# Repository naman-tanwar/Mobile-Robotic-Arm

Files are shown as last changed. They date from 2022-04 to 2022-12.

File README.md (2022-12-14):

# Mobile Robotic Arm
A 3D-printed Robotic arm mounted on Aluminium 2020 chassis which can be controlled over the internet from anywhere in the world. Ideal for remote exploration.
## Abstract
Exploration of various unreachable/hazardous places is a key to scientifically enrich our understanding of this universe. And remotely performing operations on these locations opens more aspects of not even exploration but also providing medical aid where a real human intervention is not possible. This project aims to serve this goal of remote exploration and operation.

## Methodology
The working of the project can be defined as:
- 2 Ultrasonic sensors are used to measure the distance from any obstacle in any of the four directions.
- One of the Ultrasonic sensors is mounted on a servo motor which will help to measure the distance from a obstacle in 3 directions using only one sensor
- Wheels and the robot arms are controlled using ESP32 microcontroller
- A live camera is setup using Raspberry Pi which can be accessed remotely from any location. This makes the Robot perfect for operations in remote locations.
- The robot can be controlled remotely using blynk IoT Platform

## Mechanical Design and Implementaion
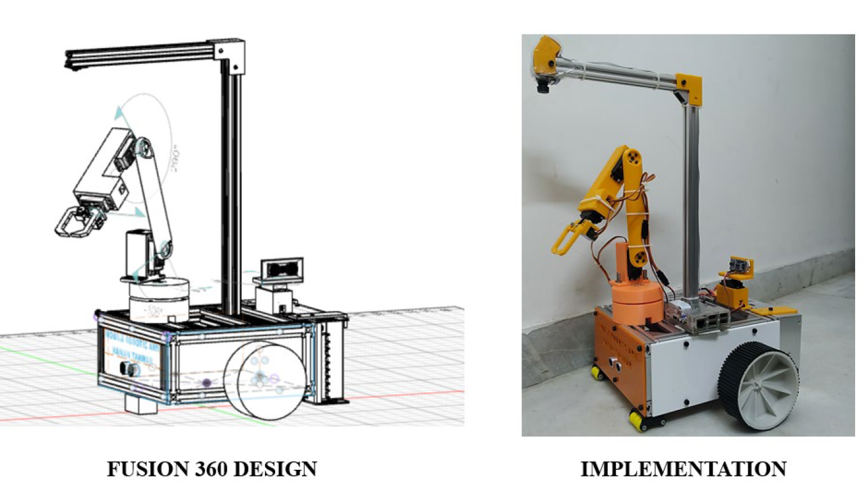
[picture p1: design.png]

## Circuit Diagram
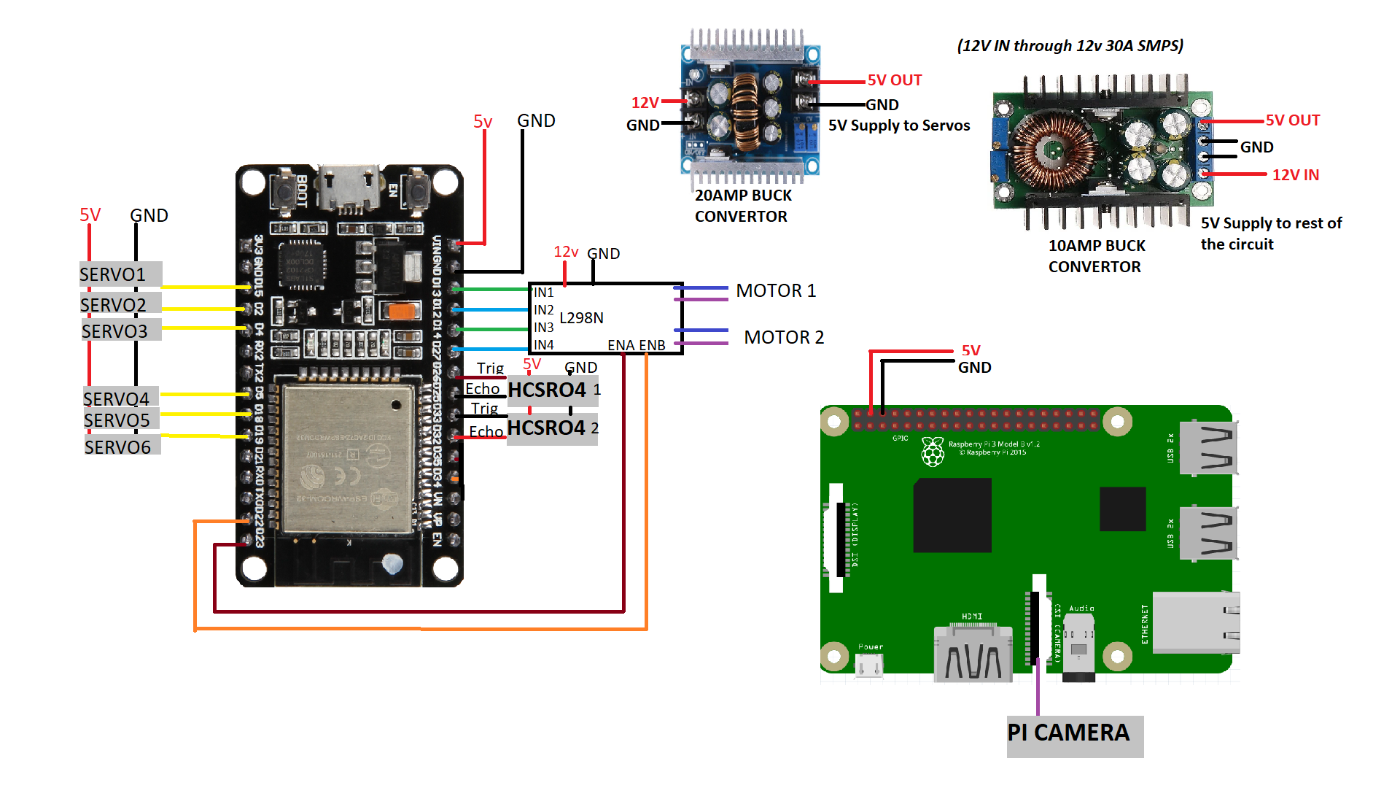
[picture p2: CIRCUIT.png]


### Power Supply
A 12V 30A rated SMPS is used to supply power to the entire system. Sisce this power supply is temporary, It can be replaced with a suitable LiPo battery (preferably, 3S 35C 3500MAh) for mobility.
The Volatage is then step down to 5v using Buck Covertors so that it can be used to power other components.
The servo (Tower Pro MG995) can pull upto 1.5A to 2A of current under stall condition. So all the 6 servers can pull upto 12A of current. Hence, a separate buck converter (rated 20A) is used to power servos alone. The remaining buck convertor (rated 10A) is used to power rest of the circuit.

### ESP32 and connected devices
ESP32 is used as a microcontroller as it has WiFi functionality which can be used to connect to the internet.
Six Tower Pro MG995 servos are connected to the digital pins of ESP32 Microcontroller (D2, D4, D5, D15, D18, D19). L298N Motor Driver is used to control two 200 RPM geared DC motor. The inputs are connected to D12, D13, D14, D27 while enable is connected to D23 and D22. Two HCSRO4 Ultrasonic senosrs are used to measure distance in all four direction. Digital Pins D25, D26, D32, D33 are used for connections of ultrasonic sensors.
### Raspberry Pi
A Raspberry Pi camera is connected to Raspberry Pi 3B+ which can be used to view camera preview remotely.
### Circuit Assembly
The circuit is made on a PCB board. Male header pins are used to connect the servo motors, Ultrasonic sensors, Motor Driver input and power input for Raspberry Pi. Femal headers are used to mount ESP 32 on the PCB.
In the top left, two Buck convertors can be seen mounted with some screws on the PCB.In the bottom, L298N motor driver is mounted with some screws.

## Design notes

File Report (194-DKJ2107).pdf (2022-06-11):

# A Custom-designed 3D Printed 4-DoF Mobile Robotic Arm for Remote Exploration

Naman Tanwar
School of Electronics Engineering Vellore Institute of Technology Vellore, Tamil Nadu, India naman.tanwar2020@vitstudent.ac.in

Sanjay Kumar Singh
School of Electronics Engineering Vellore Institute of Technology Vellore, Tamil Nadu, India sanjaykumar.singh@vit.ac.in

Abstract—Exploration of various unreachable/hazardous places is a key to scientifically enriching our understanding of this universe. And remotely performing operations on these locations opens more aspects of not even exploration but also providing medical aid where a real human intervention is not possible. This project aims to serve this goal of remote exploration and operation. A custom-designed 3D printed 4DoF Robotic arm is used for operations in the remote terrain with a movable rigid aluminum custom-designed chassis with multiple distance sensors and a camera for remote exploration and navigation.
Keywords—Robotic Arm, Mobile vehicle, Remotely Operated, ESP32, Raspberry Pi, Servo Motor, Blynk, Cloud service
I. INTRODUCTION
There are many places where human intervention is not possible simply because it might cost a human life. The requirement of intervening in those places might be to explore those parts of the world, to fix some critical faults at places where human intervention is very dangerous, to save another human life by providing medical aid, or for military reasons like spying on terrorist operations.
Hence to serve these purposes, this paper presents a project that aims to build a remotely controlled robot that can explore, navigate, operate, and can be manually controlled in such remote places.
This project is a 3D printed 4-DoF robotic arm mounted on a custom-designed Aluminium-based movable chassis with different sensors and a camera. Ultrasonic sensors are used to provide the available distance in all four directions and a camera is used to visually inspect the target on which the robot will operate. The whole construction can be controlled remotely via the internet. The only requirement is that that place should have mobile internet coverage. This can also affect the places it can operate but different modes of connectivity can be used according to the location where the robot will operate.

II. DESIGN AND IMPLEMENTAION
A. Methodology
The working of the project can be defined as:
- 2 Ultrasonic sensors are used to measure the distance from any obstacle in any of the four directions.
- The front Ultrasonic sensors will be used to measure the distance of the front obstacle. The distance can then be used by the robotic arm to operate on that obstacle
- The rear Ultrasonic sensors are mounted on a servo motor which will help to measure the distance from an obstacle in 3 directions using only one sensor
- Wheels and the robot arms are controlled using an ESP32 microcontroller
- A live camera is set up using Raspberry Pi which can be accessed remotely from any location. This makes the Robot perfect for operations in remote locations.
- The robot can be controlled remotely using the Blynk IoT Platform
Temporarily, a 12v SMPS is used instead of a LiPo battery to power the robot.
B. Mechanical Design and Implementation

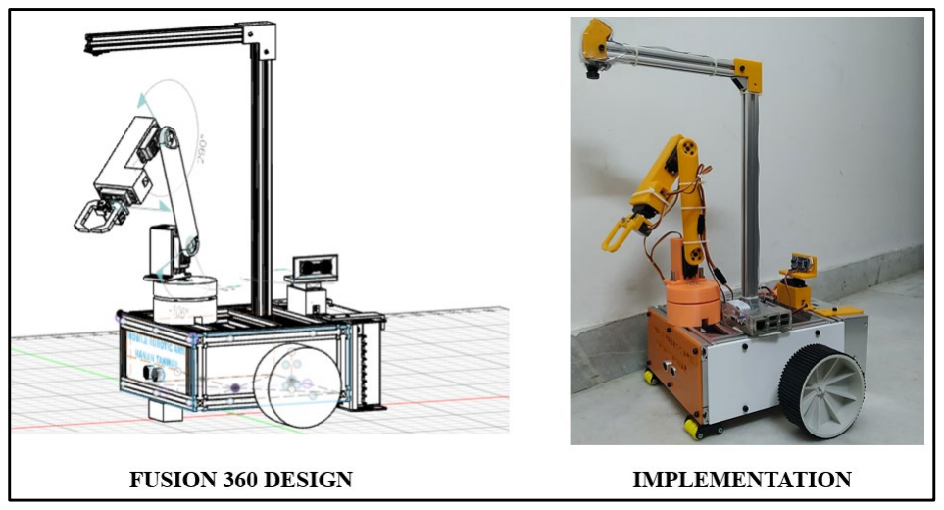
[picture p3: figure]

Fig. 1. Mechanical Design and Implementation
The complete mechanical structure is designed using Fusion 360 keeping in mind the real-world parameters such as servo motor size, motor diameter, wheel size, circuit board dimensions, power supply dimensions, the center of the movement, etc. About 14 individual parts were designed which then was 3d printed.
The robotic arm parts, sensor mount, and PCB mount were 3D printed with PLA filament.

DICKENSIAN JOURNAL

VOLUME 22, ISSUE 5, 2022

ISSN NO : 0012-2440

PAGE NO: 1764

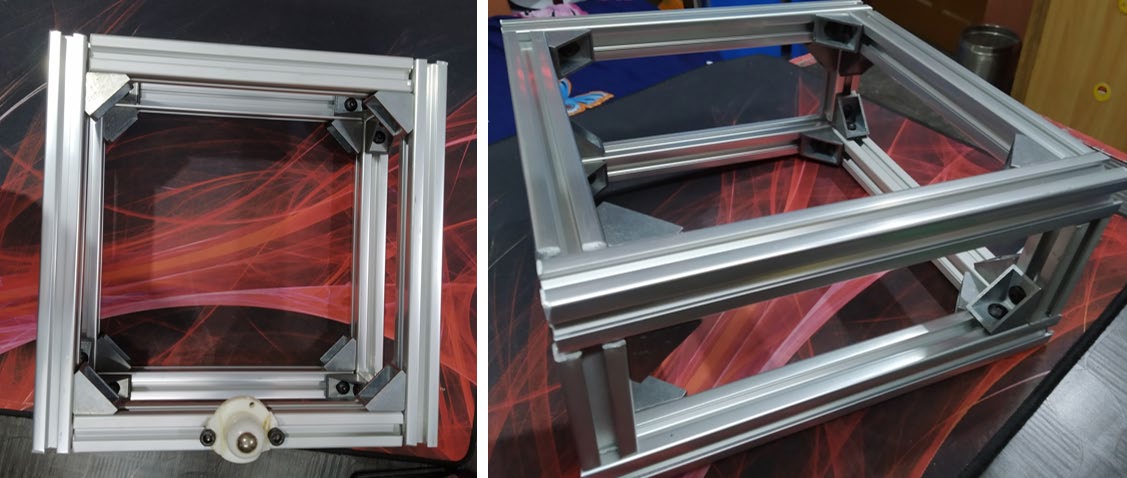
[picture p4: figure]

Fig. 2. Robot Chasis
The robot chassis was made using the 2020 Aluminium Extrusion profile. The profile was cut with an angle grinder according to the 3D design and then joined together with lead-based corner brackets. The mounts for the camera were also made using this aluminium profile.
The Camera is mounted horizontally to the ground to get a perfectly aligned 2D image of the ground which will be further useful for performing operations on the ground objects via the robotic arm.
The Orange and white colour acrylic sheet (as seen in Fig. 1) is also designed using Fusion 360 and then laser cut through an online service (www.Robu.in) to mount the front sensor and DC geared motors. [3]

Two 100rpm geared DC motors mounted on the orange acrylic sheets will be used as main motors to move the entire robot around.
Two wheels are attached to the geared motors to provide mobility. The motors with wheels are mounted horizontally centered concerning the complete chassis (this includes the width of the power supply).

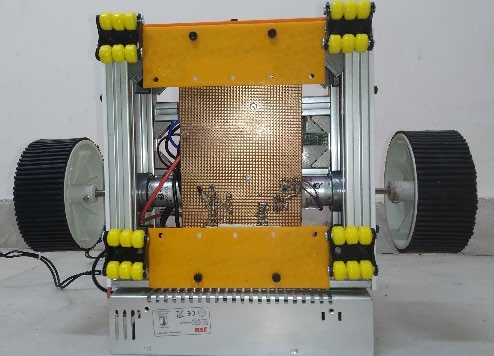
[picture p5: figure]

Fig. 3. Robot’s bottom view. 4 castor wheels, PCB board, 3D printed PCB holder plates, and 2 main 100mm wheels can be observed.
The wheel diameter is 100mm which lifted the whole chassis by 22mm and hence about 22mm castor wheels were used in front and back to provide stability to the robot
C. Circuit Diagram, Components used, and Circuit:

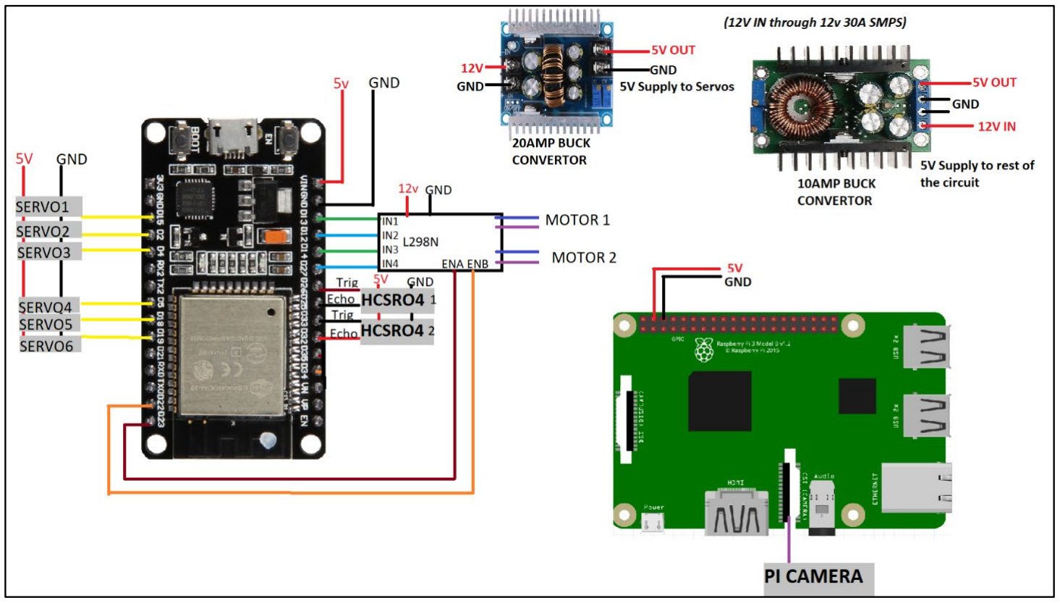
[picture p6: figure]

Fig. 4. Circuit Diagram

The Circuit has three parts:
- Power Supply
- ESP32 and connected devices
- Raspberry Pi and camera

1.Power Supply
A 12V 30A rated SMPS is used to supply power to the entire system. Since this power supply is temporary, It can be replaced with a suitable LiPo battery (preferably, 3S 35C 3500MAh) for mobility [7].
The voltage is then stepped down to 5v using Buck Converters so that it can be used to power other components.

The servo (Tower Pro MG995) can pull up to 1.5A to 2A of current under stall conditions. So all the 6 servers can pull up to 12A of current. Hence, a separate buck converter (rated 20A) is used to power servos alone. The remaining buck convertor (rated 10A) is used to power the rest of the circuit. ESP32 is used as a microcontroller as it has WiFi functionality which can be used to connect to the internet. A JioFi hotspot is used to connect to the internet. Since the JioFi hotspot is based on the mobile internet, the hotspot itself is mounted on the robot and hence there is no effect on the mobility of the robot
2.ESP32 and connected devices
Six Tower Pro MG995 servos are connected to the digital pins of the ESP32 Microcontroller (D2, D4, D5, D15, D18, D19). L298N Motor Driver is used to control two 200 RPM geared DC motors. The inputs are connected to D12, D13, D14, and D27 while enable is connected to D23 and D22. Two HCSRO4 Ultrasonic sensors are used to measure distance in all four directions. Digital Pins D25, D26, D32, and D33 are used for connections of ultrasonic sensor

3.Raspberry Pi and Camera
A Raspberry Pi camera is connected to Raspberry Pi 3B+ which can be used to view camera preview remotely.
The previously used 5v 10Amp buck convertor is used to directly power the raspberry pi through its GPIO pins.

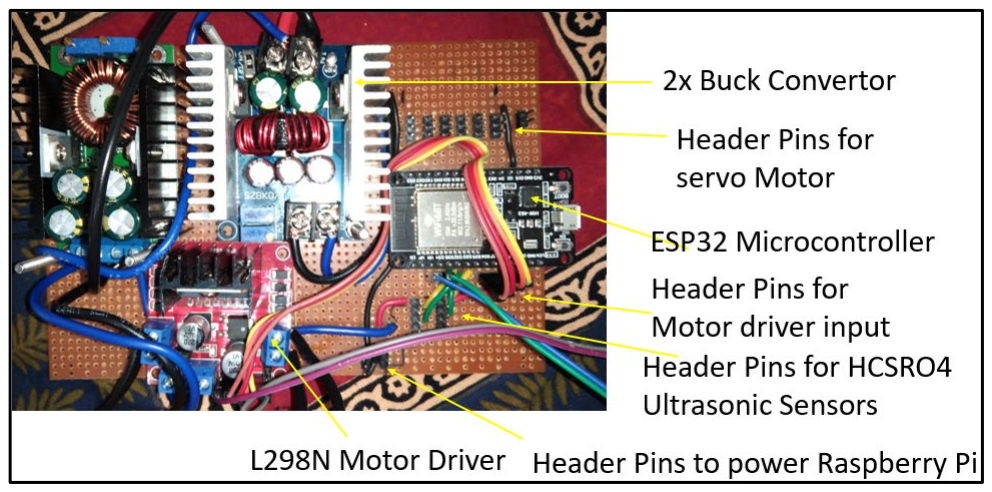
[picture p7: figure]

Fig. 5. Circuit
The circuit is made on a PCB board. Male header pins are used to connect the servo motors, Ultrasonic sensors, Motor Driver input, and power input for Raspberry Pi. Female headers are used to mount ESP 32 on the PCB.
Two Buck converters can be seen mounted with some screws on the PCB in the top left. At the bottom, the L298N motor driver is mounted with some screws.
D. Raspberry Pi Camera setup:
- A web interface is set up for the Raspberry Pi camera through an Open Source GitHub Project. But this can only be viewed locally. [2]
- Then, using the remote.it platform, the local webpage is streamed to the internet which can be accessed through a specific URL. [4]
- This URL is then used in the Blynk IoT platform to watch the video stream through the mobile app. [5]
E. Servo Calibration
- The MG995 servos used for the arm were not calibrated to move to a correct angle.
- For an input of 0 to 147 degrees (using Arduino IDE) the servo moved from 0 to 180 degrees. So, the servos were calibrated accordingly.
- The fully open and fully closed point for the servo used in the claw was found to be 180 and 140 respectively
F. Movement Equations

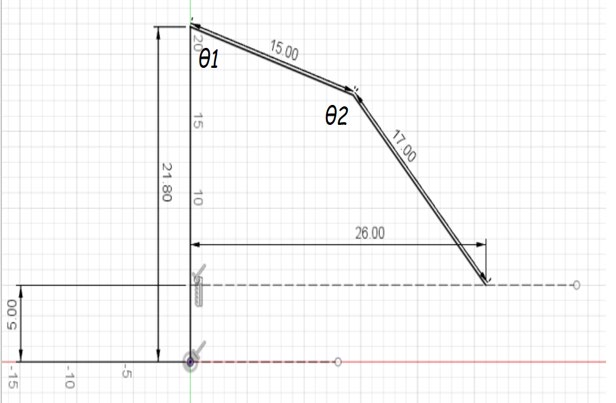
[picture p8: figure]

Fig. 6. 2D constrained sketch in Fusion 360
A 2D constrained line schematic was set up in Fusion 360. For different values of the horizontal distance, angle values were found which then was inserted into Microsoft Excel to find polynomial equations between the distance and the angle

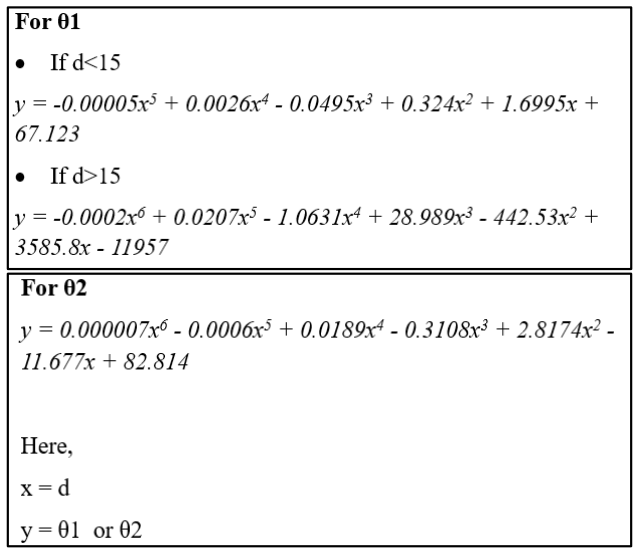
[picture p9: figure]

Fig. 7. Movement Equations

G. Mobile App using blynk

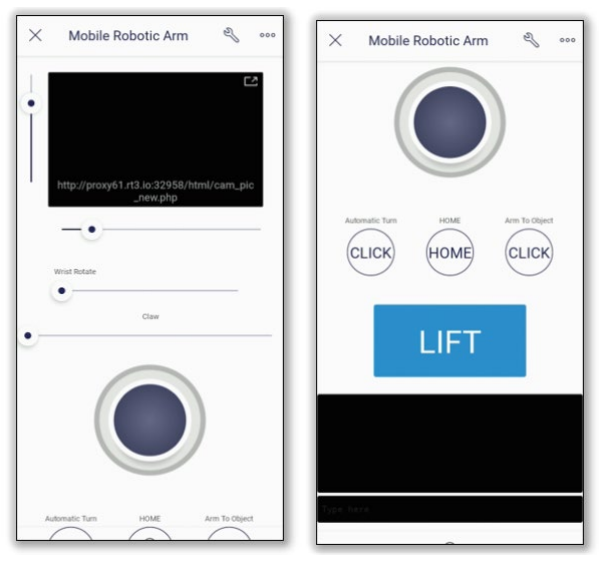
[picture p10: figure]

Fig. 8. Mobile App using Blynk IoT platform
The Blynk IoT provides IoT functionality to the robot. This platform also provides an app builder with which we can build our app using its provided widgets.
Features of our Mobile Application:
- Display for camera output
- Horizontal and Vertical Sliders to control Arm position
- Sliders to control Wrist Angle and Claw
- Joystick to move the Robot
- Buttons to perform some programmed operations such as Automatic Turn, Moving Arm to Object Location, and Home button to place arm to home location
- LIFT button to lift the arm up
- Terminal window to perform debugging.
H. ESP32 Code Flow chart and Explanation
The code for the ESP32 microcontroller is written in C++ inside Arduino IDE. Different extra libraries for the Blynk platform and servo control were also installed in the Arduino IDE. Since the code has more than 500 lines so only an explanation and flowchart are mentioned in this paper. The actual code can be viewed using the GitHub link provided in the references [1].

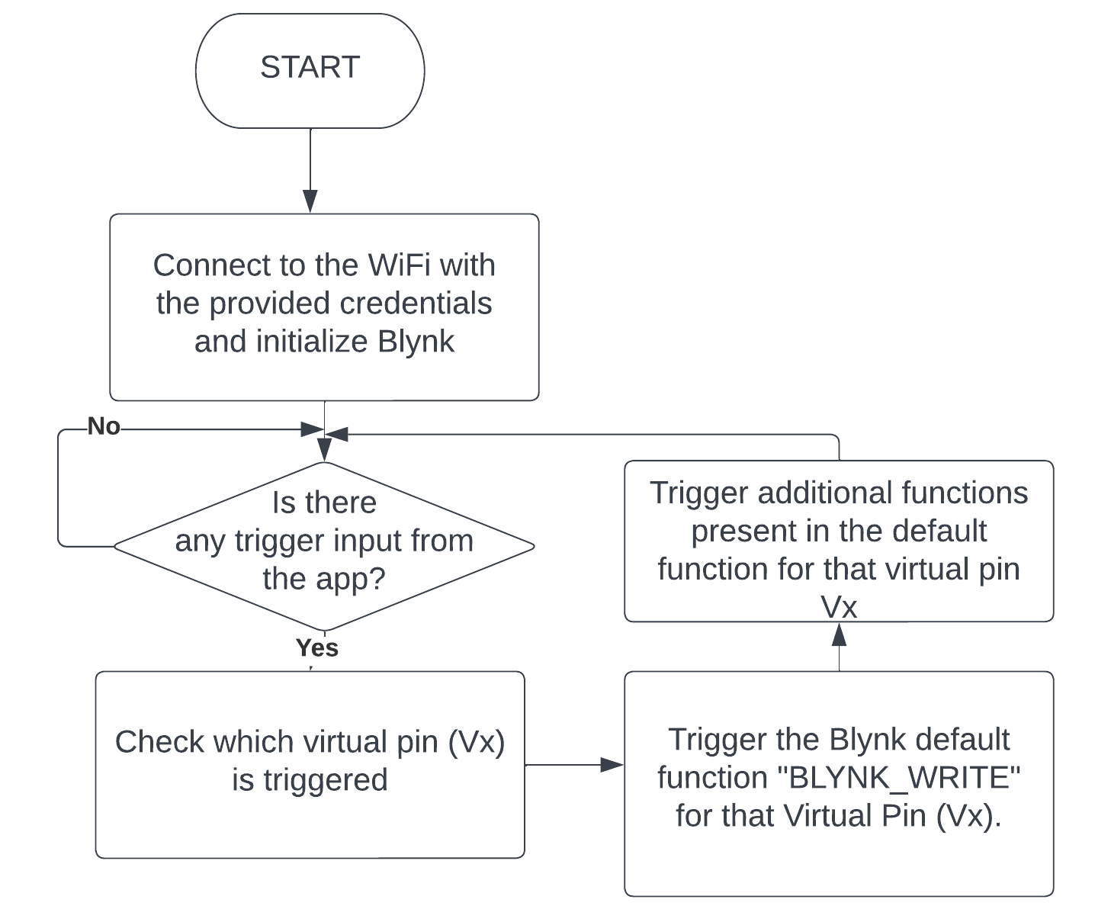
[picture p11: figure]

Fig. 9. Basic Flow Chart of the Operation
Initially, the ESP32 gets connected to the WiFi hotspot with the credentials provided in the code itself. Then the device looks for the trigger of any virtual pin through the application created using the Blynk platform.
Vx represents the Virtual Pin where ‘x’ stands for the pin-number. The various functions involved in the operation are listed in TABLE I.
TABLE I. Various Functions Triggered by the Virtual Pins and their Description
Virtual Pin/ Data Stream | Functional Description of BLYNK_WRITE (Vx) | Additional Functions Called during operation
V0 | Slider control for Base i.e., Horizontal Slider | BaseServoOperate() – Custom function to rotate base servo
V2 | Terminal Window | GetSensorData() – To get the data from both ultrasonic sensors
V3 | Joystick Control | FrontDist() – To get front sensor destance data forward(), backward(), right(), left(), Brake() – These functions control the 6 pins of the motor driver which then controls the 2 motors.
V4 | Vertical Slider | calcTheta(vertValue) – This will calculate theta based on the value of the vertical slider according to the formulae derived earlier.

V5 | Slider to Rotate Wrist | WristServoOperate() – To operate the wrist servo based on the slider value
V6 | Slider to operateClaw | ClawServoOperate() - To operate claw servo based on the slider value
V7 | Home Button | Home() – To make the servo go home positions as defined in the code.
V8 | AutoTurn Button | autoTurn() – This will initially calculate the distance in all 4 directions and then decide to rotate in the preferred direction.
V9 | ArmToObject Button | FrontDist() – To obtain a front distance value from the sensor calcTheta()- To calculate theta values based on the front sensor and then operate the servos BaseServoOperate() – To operate base servo
V10 | Lift Button | ArmServoOperate() – To rotate the servo based on the two angle values

III. WORKING DEMONSTRATION
A. Automatic Arm Movement Towards object

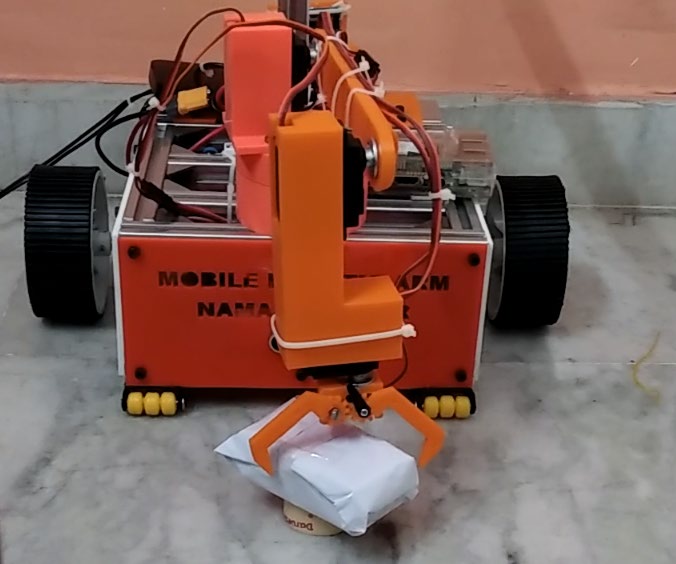
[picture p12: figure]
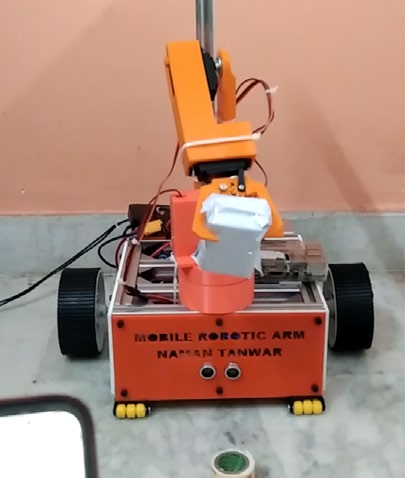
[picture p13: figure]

Fig. 10. Automatic Arm Movement and Object Lifting
When the ArmToObject button is pressed, the front Sensor finds the distance of the object from the robot which then is used to move the robotic arm. Then the object can be lifted just by clicking on the LIFT button on the mobile application.
B. Sensor readings through debug window

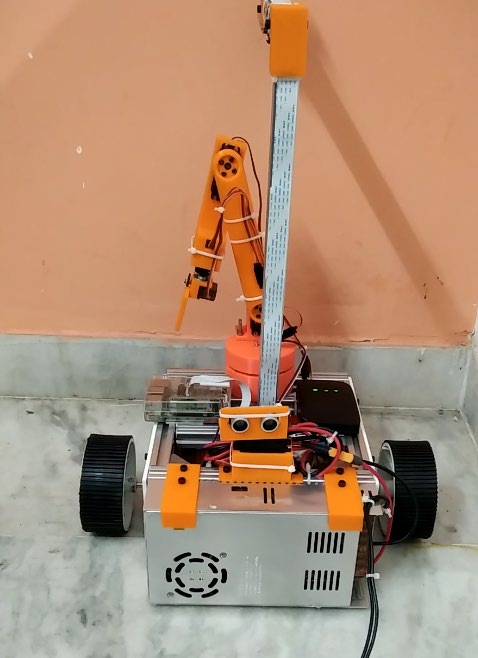
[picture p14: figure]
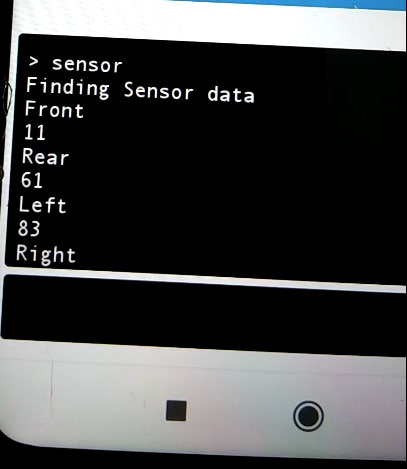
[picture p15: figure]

Fig. 11. Robot State and Sensor Readings
The robot is programmed as such if you enter “sensor” in the debug window then the robot will find the distance in all 4 directions and then displays it on the debug window itself.
C. Automatic Turn

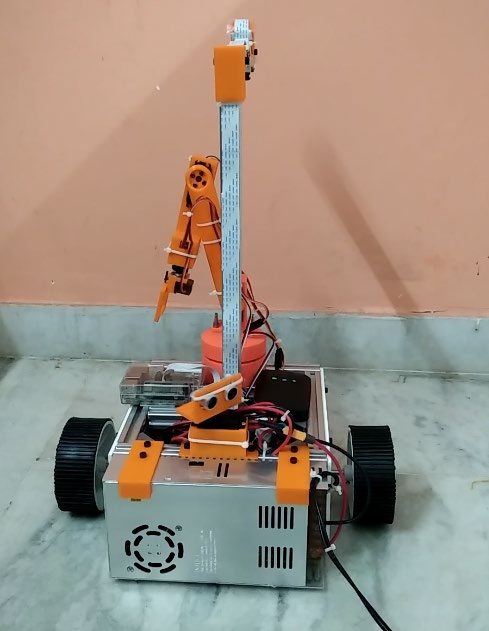
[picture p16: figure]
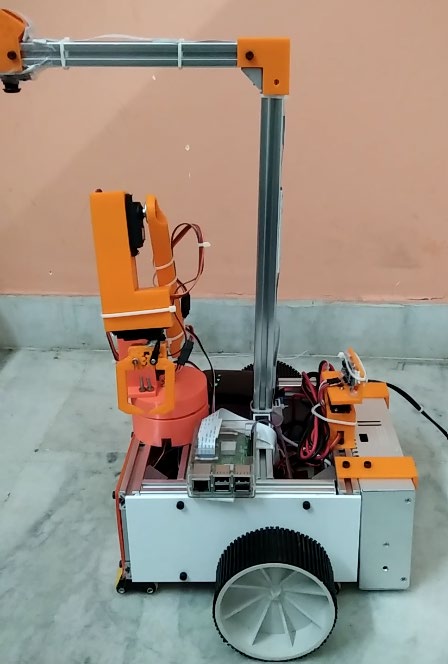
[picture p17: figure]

Fig. 12. Robot initial State and State after Turn Operation
When the Automatic Turn button is pressed, the robot will first find the distances in all 4 directions and then turn Right or Left based on the amount of distance available.
It was found out that when both the motors are spinning in the same rotational direction (clockwise/anticlockwise) with the same base speed (ie ~100rpm at ~12v), then it takes exactly 600ms to make a perpendicular rotation. Hence to turn left or right the motors were programmed to spin in clockwise or anticlockwise respectively for exactly 600ms. The entire robot’s operation can be viewed through the demonstration videos which can be viewed through the Google Drive link shared. [6]

IV. SUMMARY
In this paper, a practical model of the Mobile Robotic Arm was discussed. Initially, the complete robot was designed using Fusion 360 from which some parts were 3D printed including the parts for the Arm of the robot and structural support parts like PCB holder and power supply holder. The design gave an idea of how the real-world robot will look like and it also helped in constructing the Aluminum 2020 profile-based chassis and gave a layout for laser cutting the 3 acrylic sheets which were then used to mount the ultrasonic sensor and the motors
Then circuit was designed and built on a PCB board (Veroboard) keeping in mind the power requirements of every component. Temporarily a 12v SMPS was used which can easily be replaced with a suitable LiPo battery in the future.
Then the movement equations were practically derived, different moving parts were calibrated and finally, a suitable code for the ESP32 was written in C++ with different functions like Setting arm location using Sliders, Auto Arm to Object, Arm to Home, Lift Operation, Automatic Robot Turn operation, Joystick Movement and Getting data using terminal, using Arduino IDE.
Finally, the working of the complete project was demonstrated.
V. FUTURE IMPROVEMENTS
- Using LIPO battery instead of SMPS Supply
- Using better servos (rather than stepper motors) which are more precise, have zero gear dead-zone, and can handle more weight (This may require a major design change and implementation of gear system)
- Coding an automatic area map algorithm to perform a certain task in a remote area without human intervention
- Using LIDAR instead of Ultrasonic sensors to map the area
- Using image processing to identify the object with its 3D dimensions

VI. REFERENCES AND USEFUL LINKS
[1] GitHub link to view this entire project. https://github.com/namanteg/Mobile-Robotic-Arm
[2] GitHub link for local Raspberry Camera setup: https://github.com/silvanmelchior/RPi_Cam_Web_Inter face (https://github.com/silvanmelchior/RPi_Cam_Web_Interface)
[3] Online Laser Cutting service used: https://robu.in/product/online-laser-cutting-service
[4] Blynk IoT platform website: https://blynk.io/
[5] Remote.it website: https://remote.it/
[6] Google Drive link for videos related to robot’s operation: https://drive.google.com/drive/folders/1_x- DkT6cmrkyrrUYNz0MS6p55thI3KZy?usp=sharing
[7] Battery calculator: https://www.batteriesinaflash.com/c- (https://www.batteriesinaflash.com/c-rating-calculator) rating-calculator (https://www.batteriesinaflash.com/c-rating-calculator)
[8] Russell Barnes, “Power your Raspberry Pi: expert advice for a supply”. Available at: https://magpi.raspberrypi.com/articles/power-supply
[9] Pavel Bayborodin, “How to get started with Blynk”, posted on June 15, 2021. Available at: https://blynk.io/blog/how-to-get-started-with-blynk
[10] Official Fusion 360 design guide referred. Available at: https://help.autodesk.com/view/fusion360/ENU/courses/ (https://help.autodesk.com/view/fusion360/ENU/courses/)

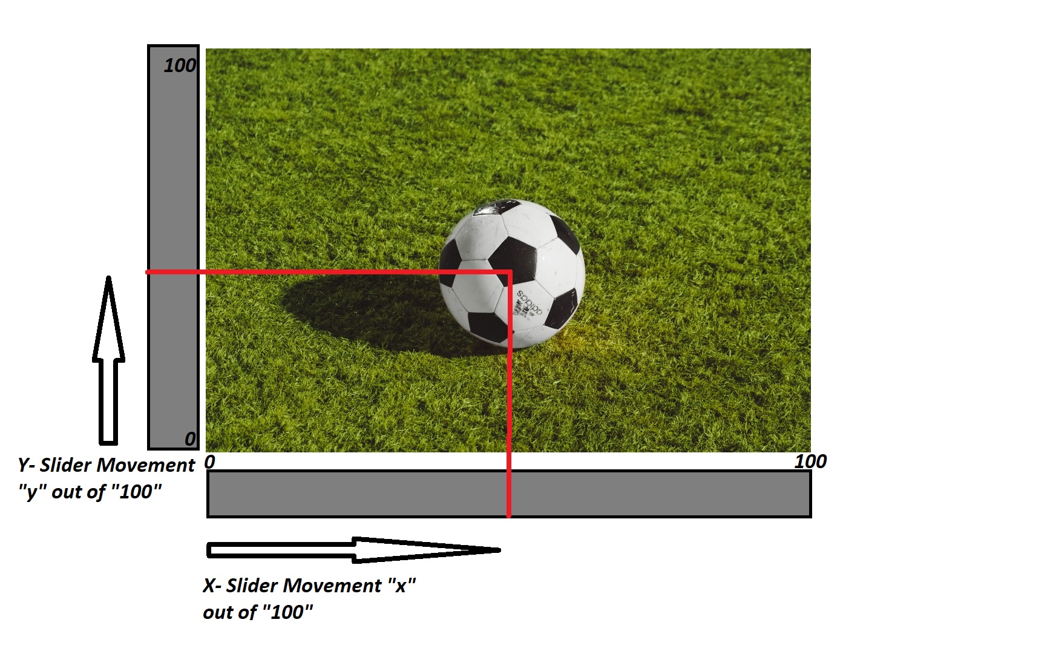
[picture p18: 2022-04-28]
Slider Working.jpg

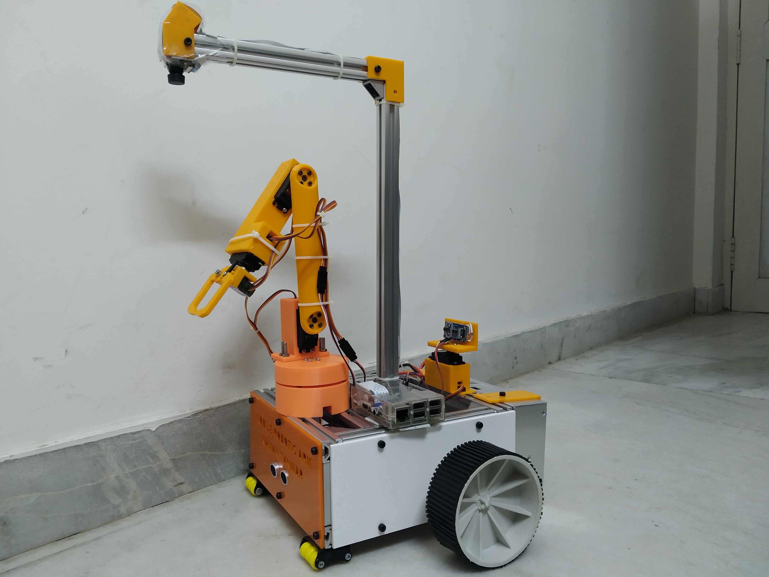
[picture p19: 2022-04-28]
img/imp.jpg

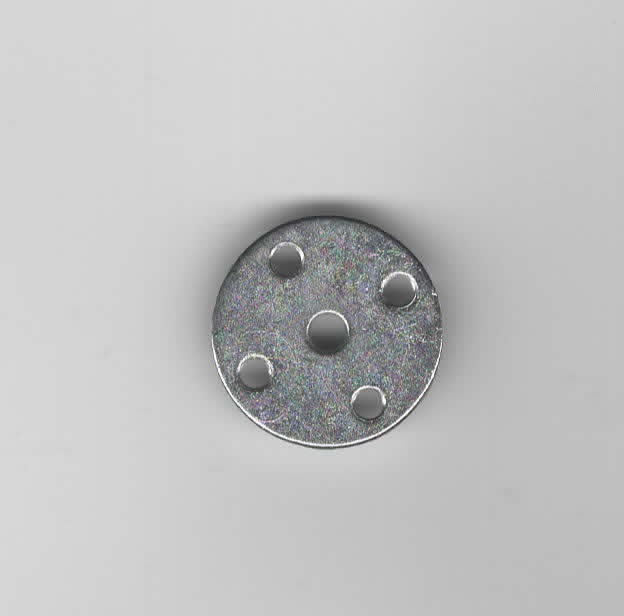
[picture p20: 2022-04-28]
img/servo nut scan.jpeg

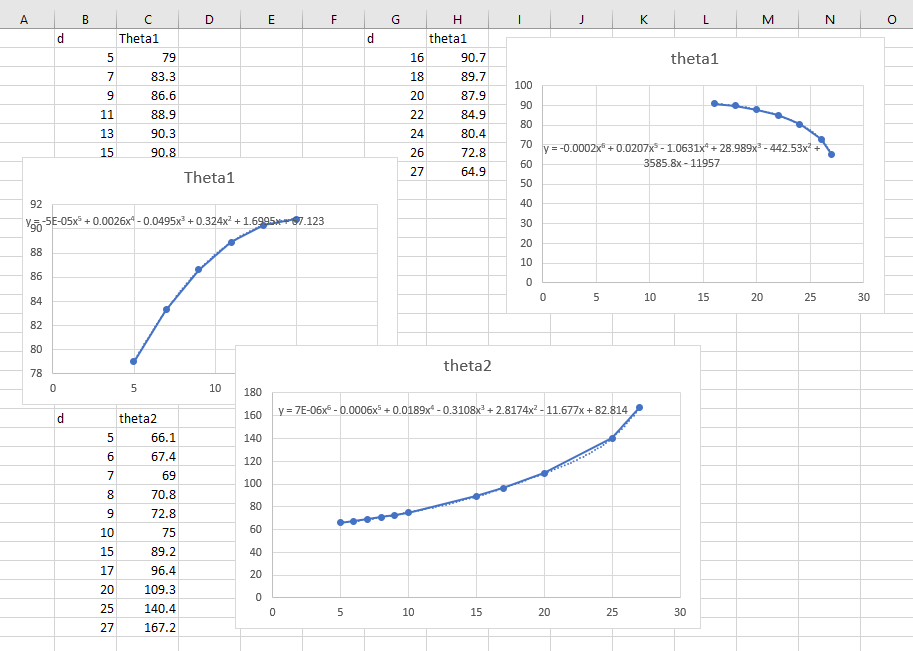
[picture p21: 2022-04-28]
excel equations.png

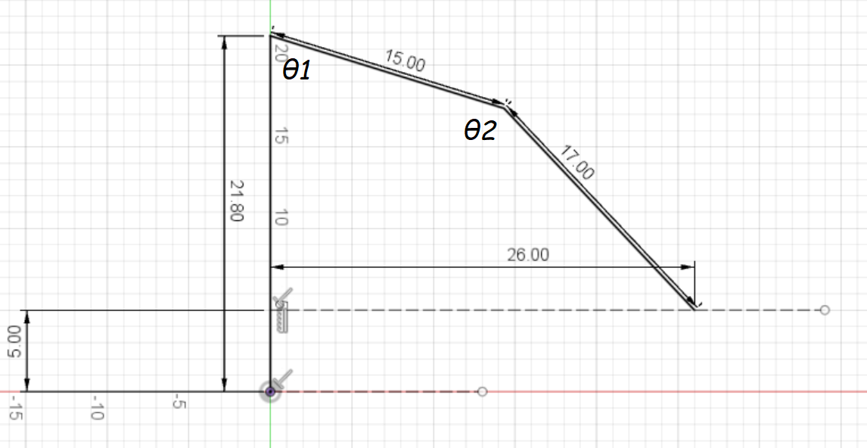
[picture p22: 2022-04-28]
motion study sketch.png

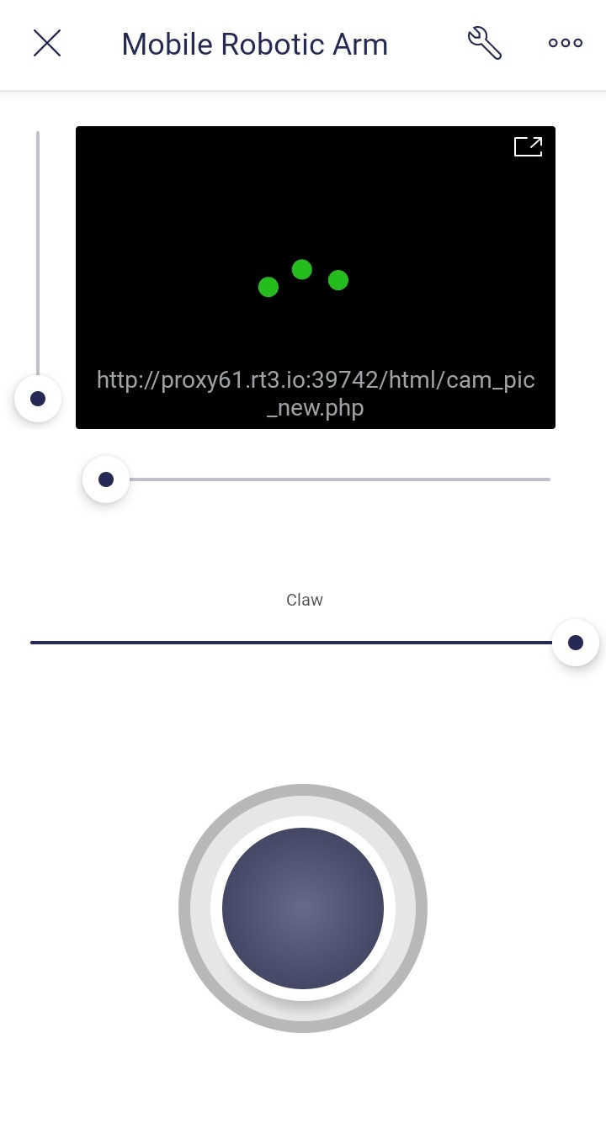
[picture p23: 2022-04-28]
img/Screenshot_2022-03-13-21-40-53-332_cloud.blynk.jpg

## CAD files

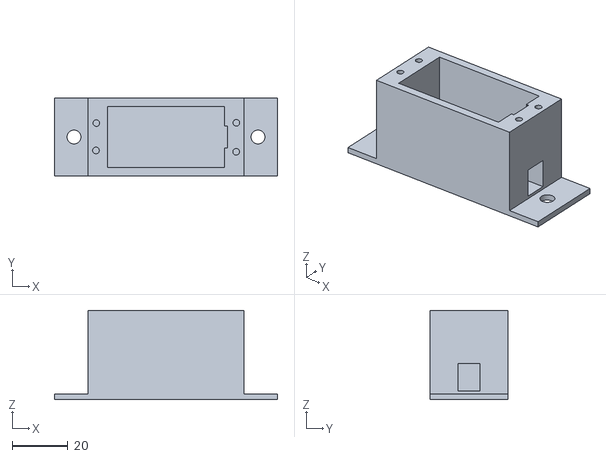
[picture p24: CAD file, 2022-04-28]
3D FILES/Top servo holder v3.stl
80.0 x 28.0 x 32.0

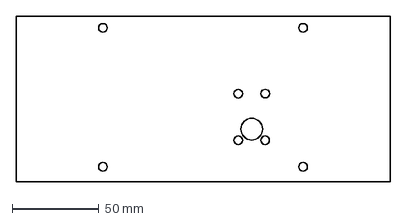
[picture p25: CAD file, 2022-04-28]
dxf sketches/FOR WHEELS.dxf
215.0 x 95.0 mm

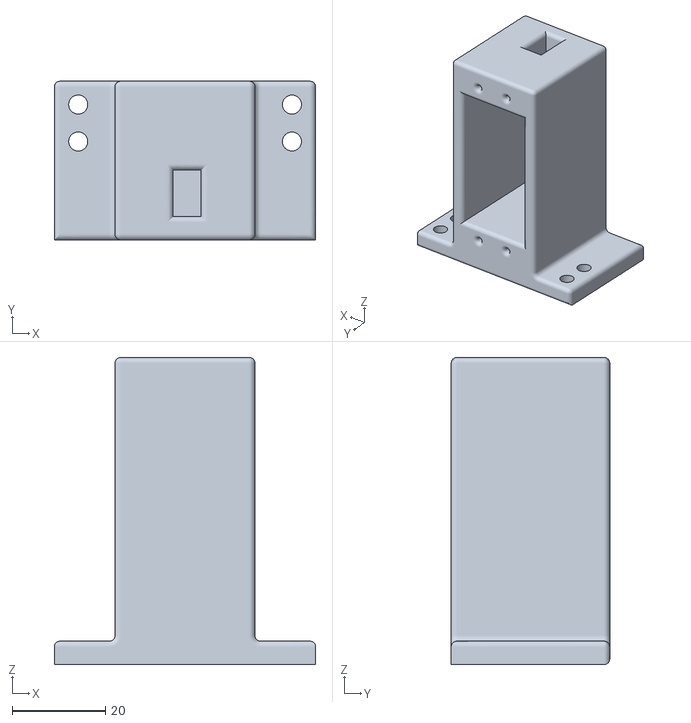
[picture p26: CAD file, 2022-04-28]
3D FILES/2nd axis bottom v15.stl
56.0 x 34.0 x 65.8

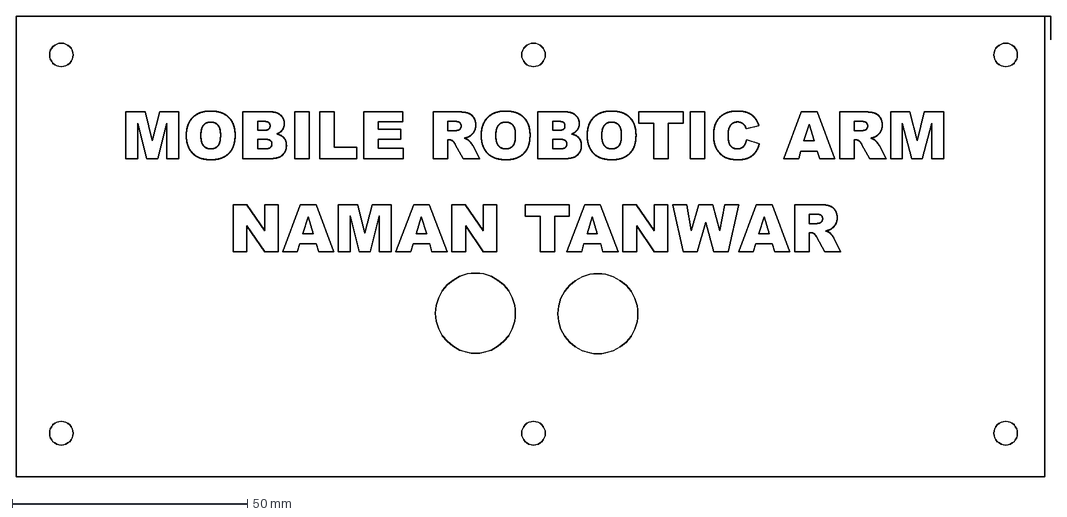
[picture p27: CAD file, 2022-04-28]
dxf sketches/FRONT.dxf
219.6 x 97.7 mm

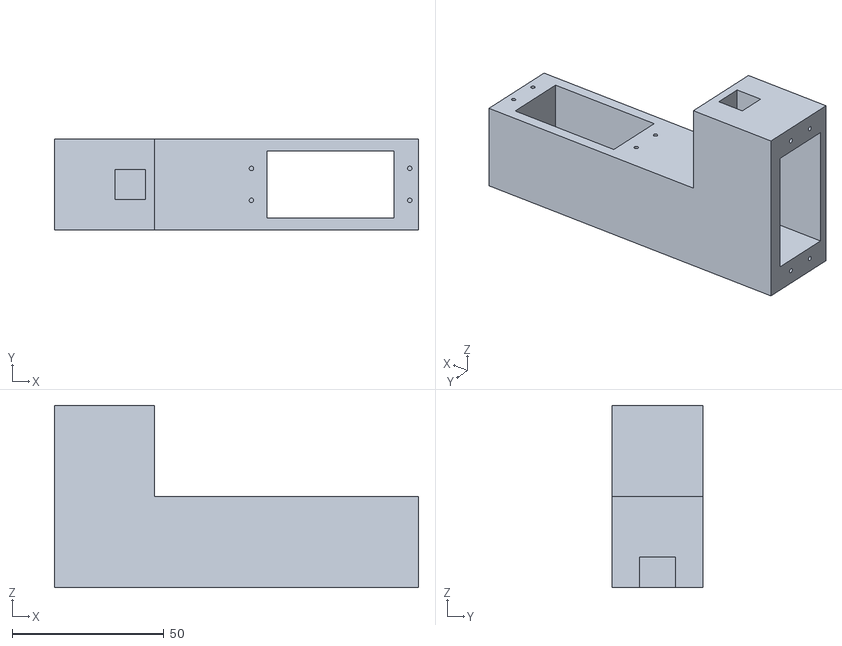
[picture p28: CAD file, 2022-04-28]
3D FILES/3d axis v9.stl
120.0 x 30.0 x 60.0

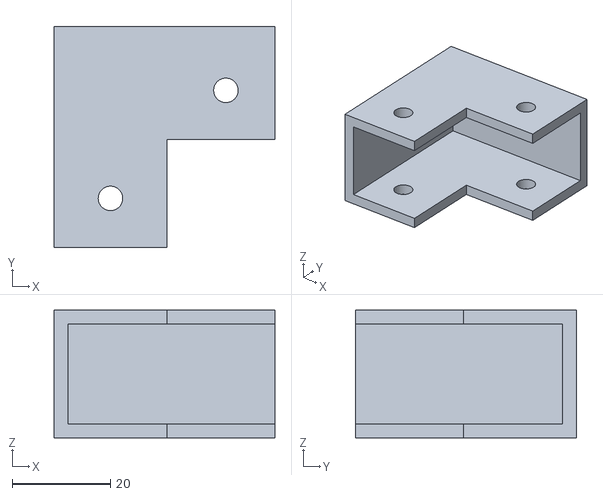
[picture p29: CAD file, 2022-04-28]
3D FILES/angle bracket v2.stl
45.0 x 45.0 x 26.0

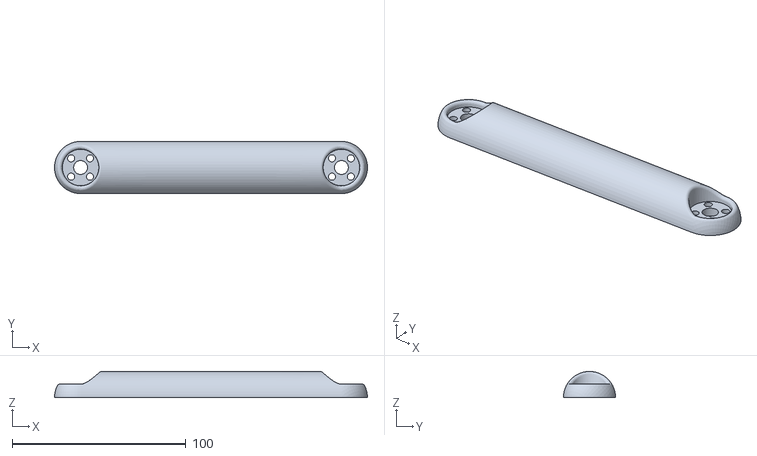
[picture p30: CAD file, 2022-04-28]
3D FILES/2nd axis arm 2nd design v3.stl
180.0 x 30.0 x 15.0

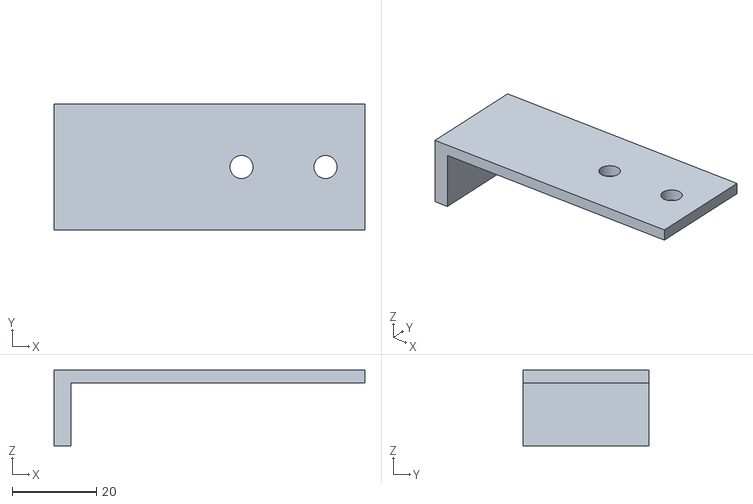
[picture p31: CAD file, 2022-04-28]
3D FILES/smps holder v3.stl
74.0 x 30.0 x 18.0

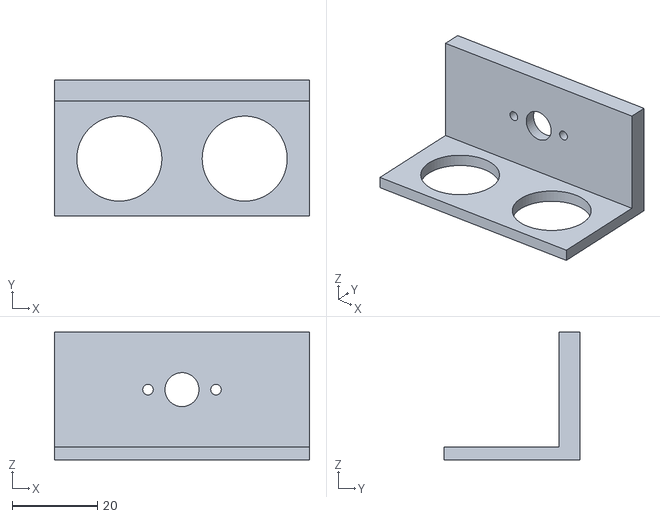
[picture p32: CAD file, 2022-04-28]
3D FILES/Ultrasonic sensor mount on servo v3.stl
60.0 x 32.0 x 30.0

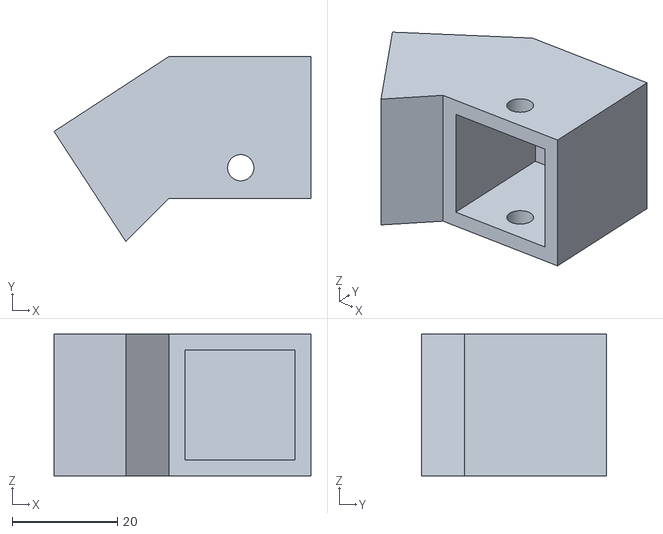
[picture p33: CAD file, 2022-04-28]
3D FILES/Cam mount v3.stl
48.9 x 35.2 x 27.0

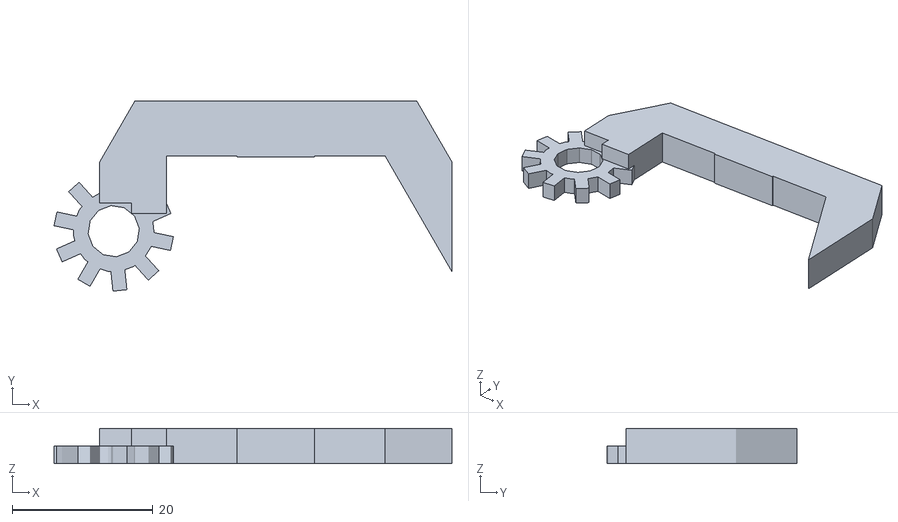
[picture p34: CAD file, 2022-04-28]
3D FILES/rightpincer.stl
56.5 x 27.0 x 5.00

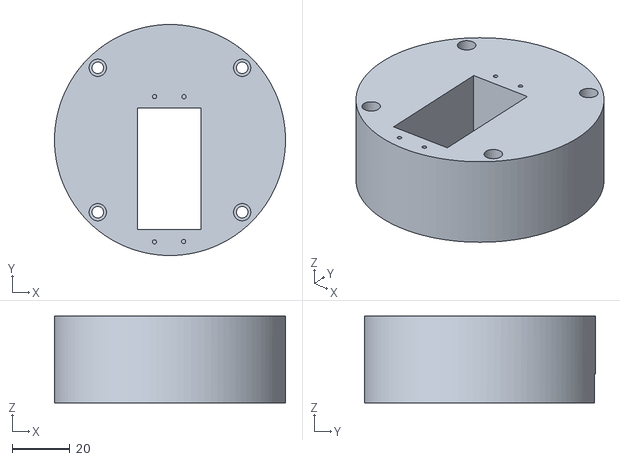
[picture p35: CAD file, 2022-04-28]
3D FILES/1st axis base v10.stl
80.0 x 80.0 x 30.0

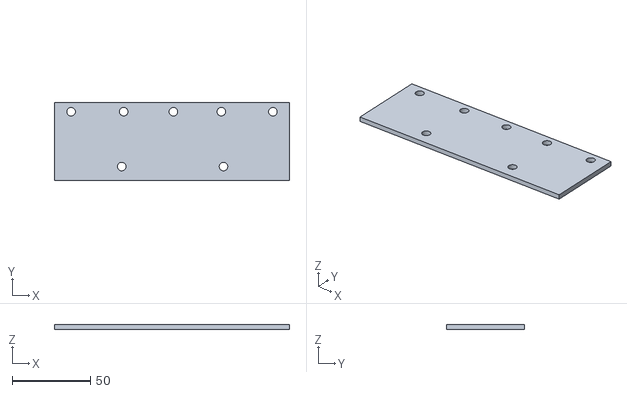
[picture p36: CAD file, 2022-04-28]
3D FILES/ckt plate v6.stl
150.0 x 50.0 x 3.00

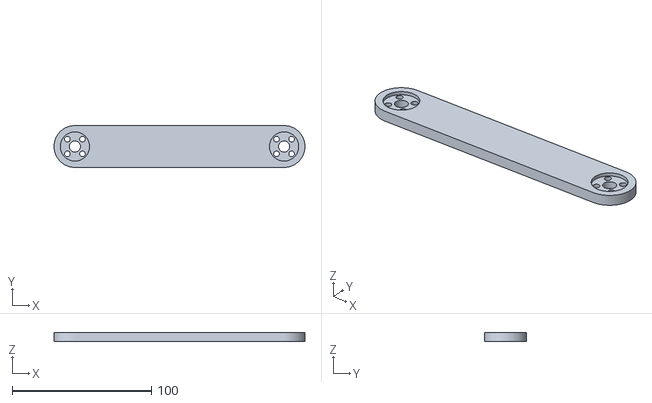
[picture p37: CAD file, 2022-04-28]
3D FILES/2nd axis arm v8.stl
180.0 x 30.0 x 6.50

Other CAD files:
3D FILES/1st axis top v10.stl
3D FILES/leftpincer.stl
3D FILES/servobox.stl

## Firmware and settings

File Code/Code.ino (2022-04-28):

/* Comment this out to disable prints and save space */
#define BLYNK_PRINT Serial

#define BLYNK_TEMPLATE_ID "TMPLu9mteHzu"
#define BLYNK_DEVICE_NAME "Mobile Robotic Arm"
#define BLYNK_AUTH_TOKEN "M06VJ8gb_LFeImP_va8tCfD8u3_2HzZX"

#include <ESP32Servo.h>
#include <WiFi.h>
#include <WiFiClient.h>
#include <BlynkSimpleEsp32.h>
#include <ESP32Servo.h>

// You should get Auth Token in the Blynk App.
// Go to the Project Settings (nut icon).
char auth[] = "M06VJ8gb_LFeImP_va8tCfD8u3_2HzZX";

// Your WiFi credentials.
// Set password to "" for open networks.
char ssid[] = "NAMAN";
char pass[] = "password";


//-----------
WidgetTerminal terminal(V2);

BlynkTimer timer;
//------------

//-----------HCSRO4 DEF
#define echoPinIN 32 
#define trigPinIN 33 
#define echoPinOUT 25
#define trigPinOUT 26 

long duration;
int FrontDistance;
int RearDistance;
int RightDistance;
int LeftDistance;

//-----END OF------HCSRO4 DEF


//-----------------
Servo myservo1; 
Servo myservo2;
Servo myservo3;
Servo myservo4;
Servo myservo5;
Servo myservo6;
//-----------------
void SensorServoOperate(int sen = 90)
{
  sen = map(sen, 0, 180, 0, 147); 
  myservo6.write(sen); //ROTATE CLAW
}
void ClawServoOperate(int claw = 160)
{
  myservo4.write(claw); //ROTATE CLAW
}
void BaseServoOperate(int rota =90)
{
  rota = map(rota, 0, 180, 0, 147); 
  myservo1.write(rota); //BASE
}
void WristServoOperate(int armrota=90)
{
  armrota = map(armrota, 0, 180, 0, 147); 
  myservo5.write(armrota); //ROTATE ARM
}

void ArmServoOperate(int t1, int t2)
{
  t1 = map(t1, 0, 180, 0, 147); 
  t2 = map(t2, 0, 180, 0, 147); 
  myservo2.write(t1); //1ST ARM
    myservo3.write(t2); //2ND ARM
    
}
    
void Home()
{
  WristServoOperate(90);
  ClawServoOperate(130);
  ArmServoOperate(20, 30);
  delay(100);
  BaseServoOperate(180);
}
int FrontDist()
{
  digitalWrite(trigPinIN, LOW);
  delayMicroseconds(2);
  digitalWrite(trigPinIN, HIGH);
  delayMicroseconds(10);
  digitalWrite(trigPinIN, LOW);
  duration = pulseIn(echoPinIN, HIGH);
  return (duration * 0.034 / 2);
}
int BackDist()
{
  digitalWrite(trigPinOUT, LOW);
  delayMicroseconds(2);
  digitalWrite(trigPinOUT, HIGH);
  delayMicroseconds(10);
  digitalWrite(trigPinOUT, LOW);
  duration = pulseIn(echoPinOUT, HIGH);
  return (duration * 0.034 / 2);
}
void GetSensorData()
{
  //---FRONT
  FrontDistance = FrontDist(); 
  
  SensorServoOperate(90);
  delay(1000);

  //---REAR
  RearDistance =BackDist(); 
  delay(500);

  //---LEFT
  SensorServoOperate(0);
  delay(1000);
  LeftDistance = BackDist(); 

  
  //--RIGHT
  SensorServoOperate(180);
  delay(1000);
  RightDistance = BackDist(); 

  delay(500);
  SensorServoOperate(90);

  Serial.println("Distance: ");
  Serial.println(FrontDistance);
  Serial.println(RearDistance);
  Serial.println(LeftDistance );
  Serial.println(RightDistance);
  
}


//-------------------Motor Control Functions
void forward()
{
  digitalWrite(23, HIGH);
  digitalWrite(22, HIGH);
  
  digitalWrite(13, LOW);
  digitalWrite(12, HIGH);
  digitalWrite(14, HIGH);
  digitalWrite(27, LOW);
}
void backward()
{
  digitalWrite(23, HIGH);
  digitalWrite(22, HIGH);
  
  digitalWrite(13, HIGH);
  digitalWrite(12, LOW);
  digitalWrite(14, LOW);
  digitalWrite(27, HIGH);
}
void right()
{
  digitalWrite(23, HIGH);
  digitalWrite(22, HIGH);
  
  digitalWrite(13, LOW);
  digitalWrite(12, HIGH);
  digitalWrite(14, LOW);
  digitalWrite(27, HIGH);
}
void left()
{
  digitalWrite(23, HIGH);
  digitalWrite(22, HIGH);
  
  digitalWrite(13, HIGH);
  digitalWrite(12, LOW);
  digitalWrite(14, HIGH);
  digitalWrite(27, LOW);
}
void Brake()
{
  digitalWrite(23, LOW);
  digitalWrite(22, LOW);
}


//-------END OF------------Motor Control Functions


//------------------ CALCULATE THETA AND OPERATE SERVOS
double ya,z;
int theta1,theta2;
String Serialt1="";
String Serialt2="";
String Serialt3="";
void calcTheta(int dist)
{
  int calibration=5;
  int x = dist + calibration;

  //-------for theta1
  if(x<=15)
  {
    ya = -0.00005*pow(x,5) + 0.0026*pow(x,4) - 0.0495*pow(x,3) + 0.324*pow(x,2) + 1.6995*x + 67.123;
  }
  else if(x>15)
  {
    ya = -0.0288*pow(x,3) + 1.5939*pow(x,2) - 30.017*x + 281.15;

  }
  theta1= (int)ya;
  theta1 = 180 - theta1;
  
  //-------for theta2
 // z = 0.000007*pow(x,6) - 0.0006*pow(x,5) + 0.0189*pow(x,4) - 0.3108*pow(x,3) + 2.8174*pow(x,2) - 11.677*x + 82.814;
z= 0.0089*pow(x,3) - 0.2351*pow(x,2) + 4.1228*x + 49.064;
  theta2= (int)z;
  
  Serialt1 = String(theta1);
  Serialt2 = String(theta1);
  Serialt3 = String(x);
  Serial.println("D= "+Serialt3);
  Serial.println("Theta1= "+Serialt1);
  Serial.println("Theta2= "+Serialt2);
  ArmServoOperate(theta1,theta2);
}
//---------END OF--------- CALCULATE THETA AND OPERATE SERVOS

//-------------------Auto Turn
void autoTurn()
{
  int perpendicularTurnTime = 600;
  terminal.clear();
  GetSensorData();
  if( FrontDistance>=20 && RearDistance>=20 && LeftDistance>=20 && RightDistance>=20)
  {
    //finding greater distance
    if(RightDistance>=LeftDistance)
    {
      terminal.println("Turning Right");
      right();
      delay(perpendicularTurnTime);
      Brake();
    }
    else
    {
      terminal.println("Turning Left");
      left();
      delay(perpendicularTurnTime);
      Brake();
    }
  }
  else
  {
    terminal.println("Insufficient Space!!!");
    Serial.println("Insufficient Space!!!");
  }
  terminal.flush();
}

//----------END OF---------Auto Turn

//--------Base Servo
int baseValue=0;
BLYNK_WRITE(V0)
{
  baseValue = param.asInt(); 
  baseValue = map(baseValue, 0, 100, 130, 50); 
  BaseServoOperate(baseValue);
}

//---END OF-----Base Servo

//------------------------VertSlider for dist to angle
double vertValueD;
int vertValue;
BLYNK_WRITE(V4)    //VertSlider for dist to angle
{
  vertValueD = param.asDouble(); 
  vertValueD *= 100;
  vertValue = (int)vertValueD;
  vertValue = map(vertValue, 0, 100, 0, 23); 
  if(baseValue>=50 && baseValue<=130)
  {
  calcTheta(vertValue);
  }
  else
  {
  BaseServoOperate(90);
  delay(500);
  calcTheta(vertValue);
  }

  Serial.println(vertValue);
}
//-------END OF-----------------VertSlider for dist to angle



//--------Wrist Servo
int wristValue;
BLYNK_WRITE(V5)
{
  wristValue = param.asInt(); 
  wristValue = map(wristValue, 0, 100, 0, 180); 
  WristServoOperate(wristValue);
}

//---END OF-----Wrist Servo


//--------Claw Servo
int ClawValue;
BLYNK_WRITE(V6)
{
  ClawValue = param.asInt(); 
  ClawValue = map(ClawValue, 0, 100, 180, 120); 
  ClawServoOperate(ClawValue);
}

//---END OF-----Claw Servo

//---------HOME
BLYNK_WRITE(V7)
{
  int HomebuttonState = param.asInt();
  if(HomebuttonState==1)
  {
    baseValue=0;
    Home();
  }
}
//---END OF-----
//-----autoTurnBtn
BLYNK_WRITE(V8)
{
  int autoBtnState;
  autoBtnState = param.asInt(); 
  if(autoBtnState==1)
  {
    autoTurn();
  }
}
//--END OF---autoTurnBtn


//-----ArmToObject
BLYNK_WRITE(V9)
{
  int armBtnState;
  int frontDist;
  armBtnState = param.asInt(); 
  if(armBtnState==1)
  {
    //Calculate Front Distance
    frontDist = FrontDist(); 
    
    //IF 5<=front dist<=23
    if(frontDist>=5 && frontDist<=23)
    {
      //calc theta and move but first check if the arm is at correct position or not
      if(baseValue>=50 && baseValue<=130)
      {
        ClawServoOperate(180);
        calcTheta(frontDist);
        }
        else
        {
          BaseServoOperate(90);
          delay(500);
          ClawServoOperate(180);
          calcTheta(frontDist);
          }
    }
    else
    {
      terminal.println("Out Of Arm Reach");
    }
    terminal.flush();
  }
}
//--END OF---ArmToObject

//-------------------Lift Object
BLYNK_WRITE(V10)
{
  int liftBtnState;
  liftBtnState = param.asInt(); 
  if(liftBtnState==1)
  {
    ArmServoOperate(10, 50);
  }

}
//-------END OF------------Lift Object


BLYNK_WRITE(V2)
{


  if (String("sensor") == param.asStr()) {
    terminal.println("Finding Sensor data") ;
    GetSensorData();
    terminal.println("Front") ;
    terminal.println(FrontDistance) ;
    terminal.println("Rear") ;
    terminal.println(RearDistance) ;
    terminal.println("Left") ;
    terminal.println(LeftDistance) ;
    terminal.println("Right") ;
    terminal.println(RightDistance) ;
  }
  else {

    // Send it back
    terminal.print("You said:");
    terminal.write(param.getBuffer(), param.getLength());
    terminal.println();
  }

  // Ensure everything is sent
  terminal.flush();
}


//-------------------------- Joystick motor control
BLYNK_WRITE(V3) {
  int x = param[0].asInt();
  int y = param[1].asInt();
  int fDist;

  // Do something with x and y
  Serial.print("X = ");
  Serial.print(x);
  Serial.print("; Y = ");
  Serial.println(y);
// for front and back movement
if(y>=200)
{
  fDist=FrontDist();
  delay(100);
  terminal.println(fDist);
  if(fDist<=30)
  {
    Brake();
    Serial.print("Brake!! Obstacle in Front");
    terminal.println("Brake!! Obstacle in Front");
  }
  else
  {
    forward();
    Serial.print("Forward");
  }

}
else if(y<=50)
{
  backward();
  Serial.print("backward");
}

// for right left movement
if(x>=200)
{
  right();
  Serial.print("right");
}
else if(x<=50)
{
  left();
  Serial.print("left");
}

if(x==128 and y==128)
{
  Brake();
  Serial.print("brake");
}

}
//----------END OF---------------- Joystick motor control






void setup()
{
  // Debug console
  Serial.begin(9600);

  Blynk.begin(auth, ssid, pass);
//-------------motor setup
  pinMode(13, OUTPUT);
  pinMode(12, OUTPUT);
  pinMode(14, OUTPUT);
  pinMode(27, OUTPUT);
  pinMode(23, OUTPUT);
  pinMode(22, OUTPUT);
//------------end of motor setup
//----------HCSRO4 setup
  pinMode(trigPinIN, OUTPUT); 
  pinMode(trigPinOUT, OUTPUT); 
  pinMode(echoPinIN, INPUT); 
  pinMode(echoPinOUT, INPUT);
//----END OF------HCSRO4 setup

  myservo1.attach(15); 
  myservo2.attach(2);
  myservo3.attach(4);
  myservo4.attach(5);
  myservo5.attach(18);
  myservo6.attach(19);

}

void loop()
{
  Blynk.run();
  timer.run();
//Serial.println("Working");  
}
